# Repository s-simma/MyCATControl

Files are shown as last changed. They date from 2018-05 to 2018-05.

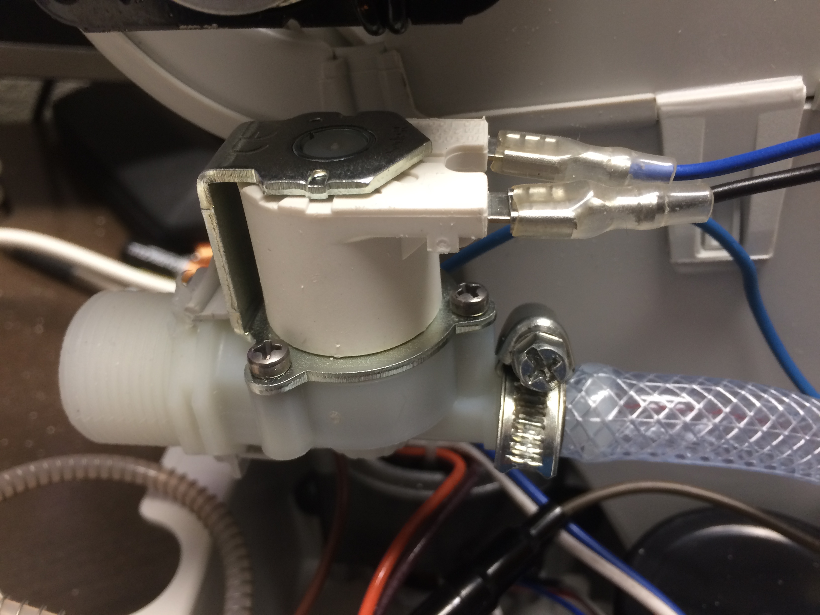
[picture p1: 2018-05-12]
images/IMG_0972.JPG

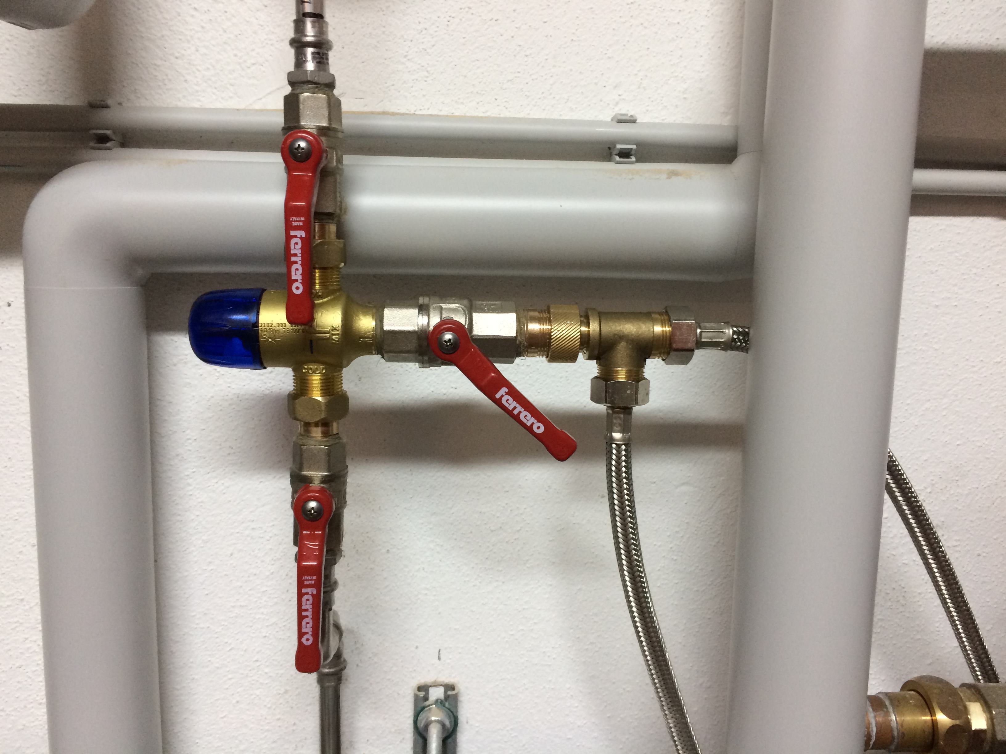
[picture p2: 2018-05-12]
images/IMG_1017.JPG

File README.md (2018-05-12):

## General ##
The reason for this project was to integrate the CAT-toilet "CATGenie120" into my smarthome and to make it possible to lock a toilet while an other one is cleaning.

**The most important for me was:**

- new board replaces the original one

- synchronice 2 or more CATGenies

- integration into my openhab2 smarthome control

- hot water for cleaning

- Using my own admixture to reduce smell

**Design of the controll board:**

- Arduino with WIFI (Genuino MKR1000)

- EEPROM for WEB-Page and cleaning programs (both can be uploaded)

- Real time clock (without power running for at least 1 day)

- Hardware watchdog

- RS485 Interface for syncronisation

##  ##

THE HARWARE DESIGN AND THE SOFTWARE IS PROVIDED "AS IS", WITHOUT WARRANTY OF ANY KIND EXPRESSED OR IMPLIED. IN NO EVENT SHALL THE AUTHOR BE LIABLE FOR ANY CLAIM, DAMAGES OR OTHER LIABILITY.

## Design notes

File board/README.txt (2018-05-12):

I ordered the board:
https://www.eurocircuits.com/

You can directly upload the Eagle .brd file (no gerber files necessary)

Advices for soldering board
---------------------------
You need 3 soldering tips
0,8mm (for IC's)
1,6mm (for resistors, small capacitors)
3,2mm (for relais, power supply, big capacitors)

solder wire 0,5mm and 1mm

a good fix mounted magnifying glass with light

1. Soilder the SMD IC's, transistors (0,8mm)
2. Soilder the SMD resistors + capacitors (1,6mm)
3. Big Components (3,2mm)

As there is nearly no space between the power supply block and the MKR1000
both shoud be soldered together. Otherwise putting the MKR1000 into the sockets could be a problem.

Important !!!!!
Some board connectors seem to be different depending where you bought the CATGenie. (Check it first)

Important !!!!!!
for 110V Version
----------------
F1, R1, R60, R61, C101, C102, C103, R100

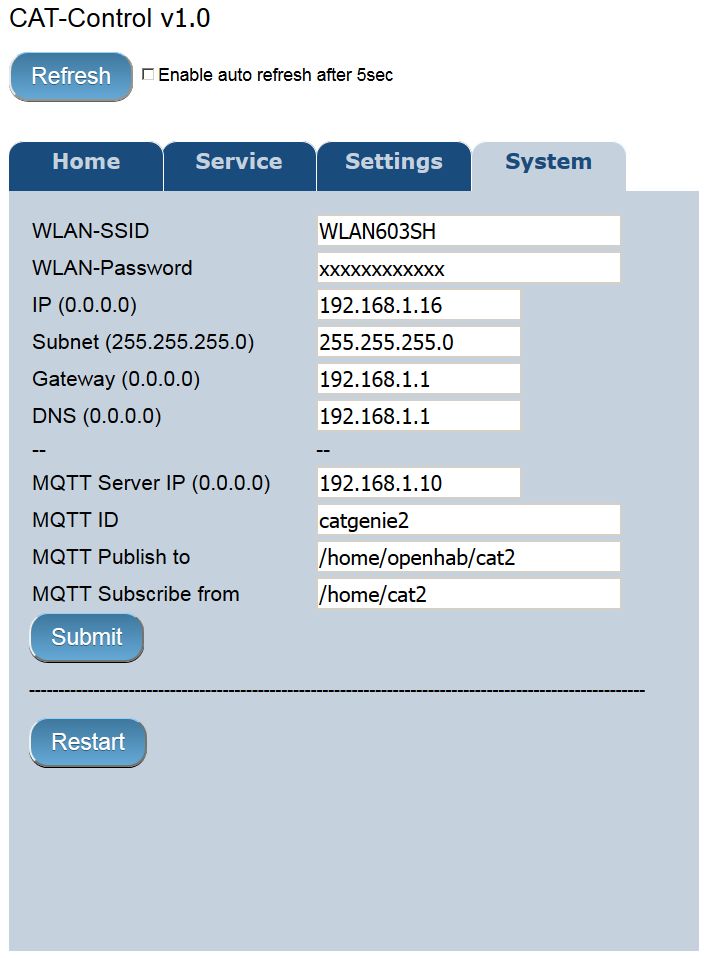
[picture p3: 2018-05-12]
images/WEB_4.jpg

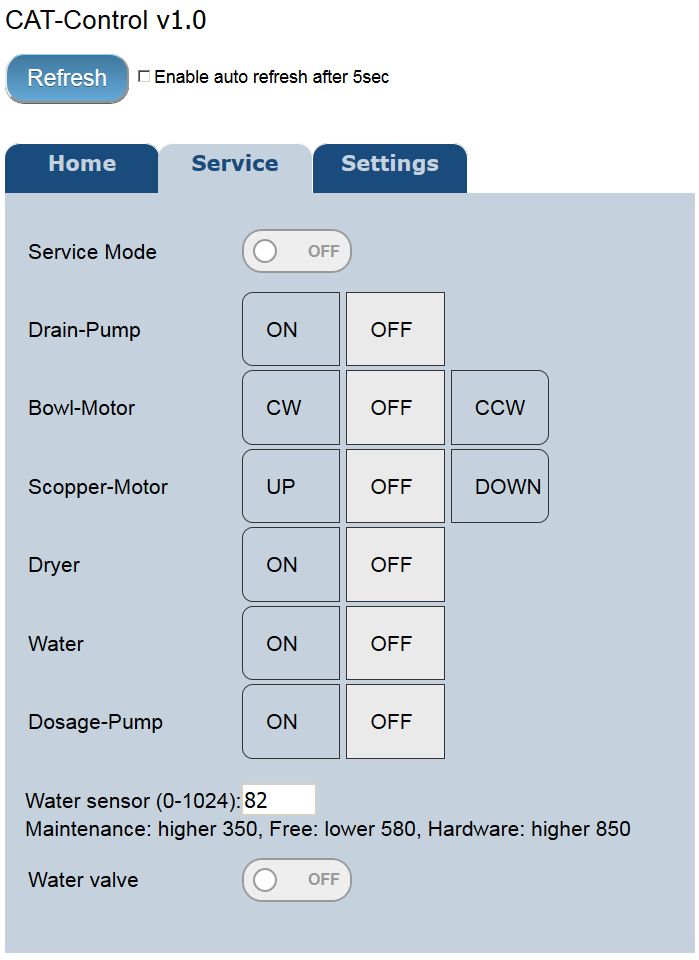
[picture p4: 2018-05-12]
images/WEB_2.jpg

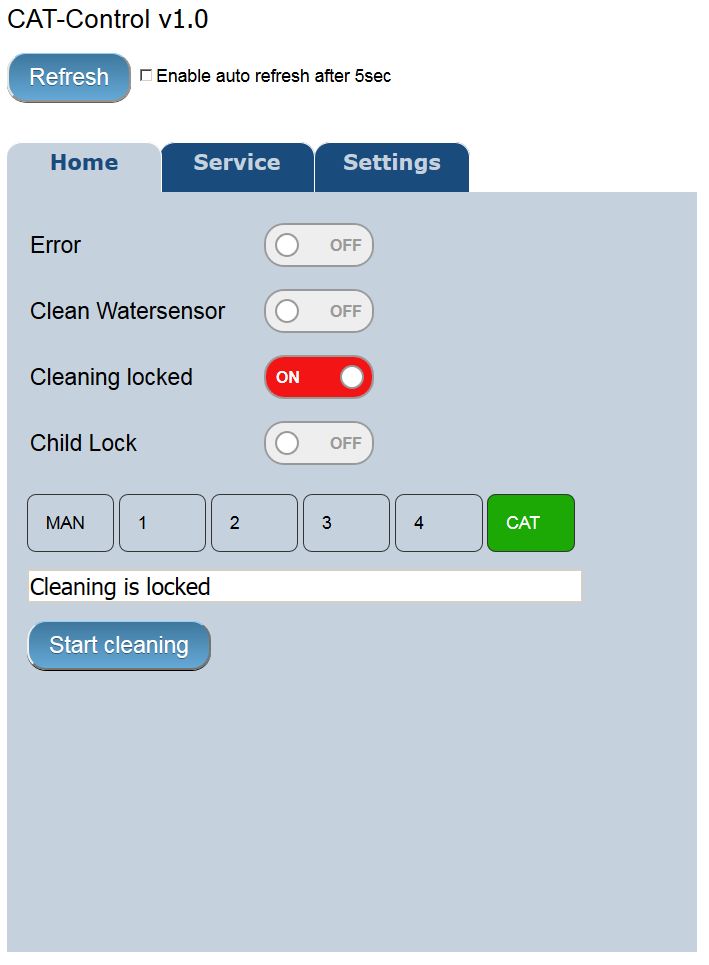
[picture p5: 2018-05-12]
images/WEB_1.jpg

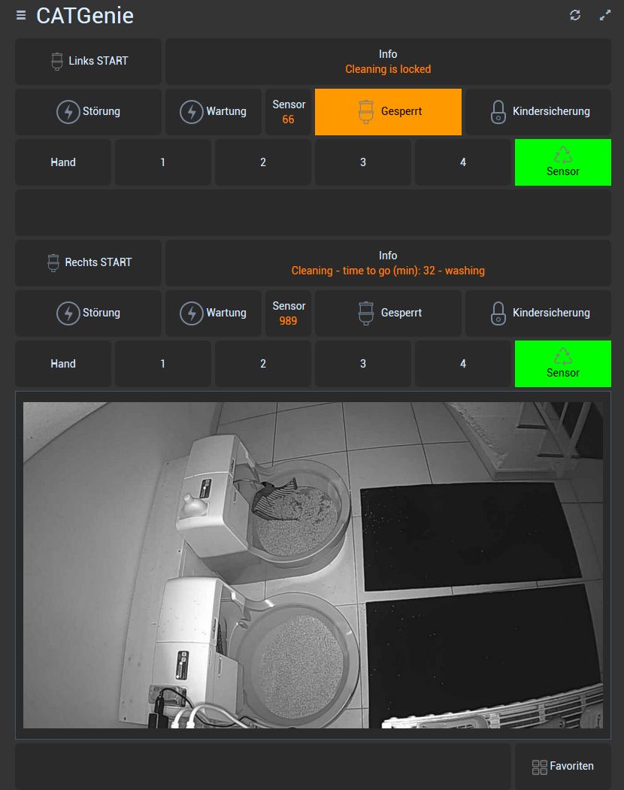
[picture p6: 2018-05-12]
images/SmartHome_4.jpg

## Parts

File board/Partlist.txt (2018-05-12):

Partlist

Exported from CatGenie120.sch at 30.04.2018 11:56

EAGLE Version 7.6.0 Copyright (c) 1988-2016 CadSoft

Assembly variant: 

Part     Value                   Device                  Package                     Library                        Sheet

+3V3                             1,6/0,8                 1,6/0,8                     wirepad                        1
+5V                              1,6/0,8                 1,6/0,8                     wirepad                        1
C1       1000UF                  EEE-FC1C221AP-CASE-G    CAPAE1030X1050N             Panasonic-EEE0_EEE1_EEE2_EEEFC 1
C2       100nF                   C1206C104K5RACTU        CAPC3216X88N                my_library1                    1
C3       47UF                    EEE-0JA470SR-CASE-C     CAPAE530X610N               Panasonic-EEE0_EEE1_EEE2_EEEFC 1
C4       100nF                   C1206C104K5RACTU        CAPC3216X88N                my_library1                    1
C5       100nF                   C1206C104K5RACTU        CAPC3216X88N                my_library1                    1
C6       100nF                   C1206C104K5RACTU        CAPC3216X88N                my_library1                    1
C7       100nF                   C1206C104K5RACTU        CAPC3216X88N                my_library1                    1
C8       100nF                   C1206C104K5RACTU        CAPC3216X88N                my_library1                    1
C9       100nF                   C1206C104K5RACTU        CAPC3216X88N                my_library1                    1
C10      10nF                    C1206C104K5RACTU        CAPC3216X88N                my_library1                    1
C11      1,5F/3,6V               SUPERCAP-RM5            SUPERCAP-RM5                my_library1                    1
C12      100nF                   C1206C104K5RACTU        CAPC3216X88N                my_library1                    1
C13      100nF                   C1206C104K5RACTU        CAPC3216X88N                my_library1                    2
C14      10nF                    C1206C104K5RACTU        CAPC3216X88N                my_library1                    1
C15      100nF                   C1206C104K5RACTU        CAPC3216X88N                my_library1                    1
C16      100nF                   C1206C104K5RACTU        CAPC3216X88N                my_library1                    1
C17      10nF                    C1206C104K5RACTU        CAPC3216X88N                my_library1                    1
C40      47UF                    EEE-0JA470SR-CASE-C     CAPAE530X610N               Panasonic-EEE0_EEE1_EEE2_EEEFC 2
C60      100nF                   C1206C104K5RACTU        CAPC3216X88N                my_library1                    2
C70      100nF                   C1206C104K5RACTU        CAPC3216X88N                my_library1                    2
C71      100nF                   C1206C104K5RACTU        CAPC3216X88N                my_library1                    2
C101     100nF/440V              ANLAUF-KONDENSATOR-RM22 ANLAUF-KONDENSATOR-RM22     my_library1                    2
C102     100nF                   ANLAUF-KONDENSATOR-RM22 ANLAUF-KONDENSATOR-RM22     my_library1                    2
C103     330nF                   ANLAUF-KONDENSATOR-RM37 ANLAUF-KONDENSATOR-RM37     my_library1                    2
D1       1N4148                  DIODE-D-5               D-5                         diode                          1
D51      1N4148                  DIODE-D-5               D-5                         diode                          2
D52      1N4148                  DIODE-D-5               D-5                         diode                          2
D53      1N4148                  DIODE-D-5               D-5                         diode                          2
D54      1N4148                  DIODE-D-5               D-5                         diode                          2
D55      1N4148                  DIODE-D-5               D-5                         diode                          2
D56      1N4148                  DIODE-D-5               D-5                         diode                          2
D57      1N4148                  DIODE-D-5               D-5                         diode                          2
D58      1N4148                  DIODE-D-5               D-5                         diode                          2
D60      1N4004                  1N4004                  DO41-10                     adafruit                       2
F1       10A                     SICHERUNGSHALTER        SICHERUNGSHALTER            my_library1                    1
GND                              1,6/0,8                 1,6/0,8                     wirepad                        1
IC1      LM393D                  LM393D                  SO08                        linear                         2
J1                               JST-EH-03-PIN           JST-EH-03-PIN               JST XH Connectors v1-0         2
J2       5267-6                  5267-6                  5267-6                      con-molex-spox                 2
J3       5267-6                  5267-6                  5267-6                      con-molex-spox                 2
J4                               KK-156-3                KK-156-3                    con-molex                      2
J5                               KK-156-2                KK-156-2                    con-molex                      2
J6       SUPU-SERIE_B_1X3        SUPU-SERIE_B_1X3        SUPU-SERIE_B_1X3            my_library1                    2
J7       JST-XH-02-PIN-ROUND-PAD JST-XH-02-PIN-ROUND-PAD JST-XH-02-PACKAGE-ROUND-PAD JST XH Connectors v1-0         2
J8       JST-XH-05-PIN-ROUND-PAD JST-XH-05-PIN-ROUND-PAD JST-XH-05-PACKAGE-ROUND-PAD JST XH Connectors v1-0         2
J9                               MOLEX-1X3               MOLEX-1X3                   my_library1                    2
J10      MOLEX-1X2               MOLEX-1X2               MOLEX-1X2                   my_library1                    1
J11                              MOLEX-1X3               MOLEX-1X3                   my_library1                    1
JP1                              JP1Q                    JP1                         jumper                         1
MKR1000                          GENUINOMKR1000          GENUINOMKR1000              my_library1                    1
MP       FLACHSTECKER-1POLIG     FLACHSTECKER-1POLIG     FLACHSTECKER-1POLIG         my_library1                    1
O1       G3VM-61G1               MOSFET_RELAIS           MOSFET-RELAIS               my_library1                    2
O2                               MOSFET_RELAIS           MOSFET-RELAIS               my_library1                    2
O3                               MOSFET_RELAIS           MOSFET-RELAIS               my_library1                    2
O4                               MOSFET_RELAIS           MOSFET-RELAIS               my_library1                    2
O5       G3VM-61G1               MOSFET_RELAIS           MOSFET-RELAIS               my_library1                    2
O6                               MOSFET_RELAIS           MOSFET-RELAIS               my_library1                    2
O7                               MOSFET_RELAIS           MOSFET-RELAIS               my_library1                    2
O8                               MOSFET_RELAIS           MOSFET-RELAIS               my_library1                    2
O60      SFH6106-3               SFH6106-3               SFH6106-3                   my_library1                    2
PH       FLACHSTECKER-1POLIG     FLACHSTECKER-1POLIG     FLACHSTECKER-1POLIG         my_library1                    1
Q1       32,768kHz               CRYSTALTC26V            TC26V                       adafruit                       1
R1       VARISTOR-7,5            VARISTOR-7,5            R-7,5                       varistor                       1
R2       10k                     WIEDERSTAND_802         WIEDERSTAND_802             my_library1                    1
R3       3.3k                    WIEDERSTAND_802         WIEDERSTAND_802             my_library1                    1
R4       3.3k                    WIEDERSTAND_802         WIEDERSTAND_802             my_library1                    1
R5       4k7                     WIEDERSTAND_802         WIEDERSTAND_802             my_library1                    1
R6       18k                     WIEDERSTAND_802         WIEDERSTAND_802             my_library1                    1
R7       18k                     WIEDERSTAND_802         WIEDERSTAND_802             my_library1                    1
R8       180R                    R-EU_M1206              M1206                       resistor                       1
R9       150R                    2NBS16-8E               SO16                        resistor-bourns                1
R10      4k7                     WIEDERSTAND_802         WIEDERSTAND_802             my_library1                    1
R11      47k                     WIEDERSTAND_802         WIEDERSTAND_802             my_library1                    1
R40      220R                    WIEDERSTAND_802         WIEDERSTAND_802             my_library1                    2
R41      560R                    WIEDERSTAND_802         WIEDERSTAND_802             my_library1                    2
R42      1k                      WIEDERSTAND_802         WIEDERSTAND_802             my_library1                    2
R43      180R                    R-EU_R1206              R1206                       rcl                            2
R44      4k7                     WIEDERSTAND_802         WIEDERSTAND_802             my_library1                    2
R45      100R                    R-EU_R1206              R1206                       rcl                            2
R46      220R                    WIEDERSTAND_802         WIEDERSTAND_802             my_library1                    2
R47      10k                     WIEDERSTAND_802         WIEDERSTAND_802             my_library1                    2
R51      270R                    R-EU_R1206              R1206                       rcl                            2
R52      270R                    R-EU_R1206              R1206                       rcl                            2
R53      270R                    R-EU_R1206              R1206                       rcl                            2
R54      270R                    R-EU_R1206              R1206                       rcl                            2
R55      270R                    R-EU_R1206              R1206                       rcl                            2
R56      270R                    R-EU_R1206              R1206                       rcl                            2
R57      270R                    R-EU_R1206              R1206                       rcl                            2
R58      270R                    R-EU_R1206              R1206                       rcl                            2
R60      13k/250V/3W             R-EU_R2512              R2512                       rcl                            2
R61      13k/250V/3W             R-EU_R2512              R2512                       rcl                            2
R62      4k7                     WIEDERSTAND_802         WIEDERSTAND_802             my_library1                    2
R63      1M                      WIEDERSTAND_802         WIEDERSTAND_802             my_library1                    2
R70      220R                    WIEDERSTAND_802         WIEDERSTAND_802             my_library1                    2
R71      560R                    WIEDERSTAND_802         WIEDERSTAND_802             my_library1                    2
R72      1k                      WIEDERSTAND_802         WIEDERSTAND_802             my_library1                    2
R73      1k                      WIEDERSTAND_802         WIEDERSTAND_802             my_library1                    2
R74      100k                    WIEDERSTAND_802         WIEDERSTAND_802             my_library1                    2
R75      47k                     WIEDERSTAND_802         WIEDERSTAND_802             my_library1                    2
R76      47k                     WIEDERSTAND_802         WIEDERSTAND_802             my_library1                    2
R77      4k7                     WIEDERSTAND_802         WIEDERSTAND_802             my_library1                    2
R78      220R                    WIEDERSTAND_802         WIEDERSTAND_802             my_library1                    2
R79      220R                    WIEDERSTAND_802         WIEDERSTAND_802             my_library1                    2
R80      560R                    WIEDERSTAND_802         WIEDERSTAND_802             my_library1                    2
R81      1k                      WIEDERSTAND_802         WIEDERSTAND_802             my_library1                    2
R82      200R                    R-EU_R1206              R1206                       rcl                            2
R83      220R                    WIEDERSTAND_802         WIEDERSTAND_802             my_library1                    2
R84      10k                     WIEDERSTAND_802         WIEDERSTAND_802             my_library1                    2
R85      4k7                     WIEDERSTAND_802         WIEDERSTAND_802             my_library1                    2
R86      4k7                     WIEDERSTAND_802         WIEDERSTAND_802             my_library1                    2
R87      47k                     WIEDERSTAND_802         WIEDERSTAND_802             my_library1                    2
R100     2,4k/3W/600V            R-STEHEND               R-STEHEND                   my_library1                    2
RL1                              G6RN-1-5VDC             G6RN-1-5VDC                 my_library1                    2
RL2                              G6RN-1-5VDC             G6RN-1-5VDC                 my_library1                    2
RL3                              G6RN-1-5VDC             G6RN-1-5VDC                 my_library1                    2
RL4                              G6RN-1-5VDC             G6RN-1-5VDC                 my_library1                    2
RL5                              G6RN-1-5VDC             G6RN-1-5VDC                 my_library1                    2
RL6                              G6RN-1-5VDC             G6RN-1-5VDC                 my_library1                    2
RL7                              G6RN-1-5VDC             G6RN-1-5VDC                 my_library1                    2
RL8                              G6RN-1-5VDC             G6RN-1-5VDC                 my_library1                    2
SG1                              PIEZZO-BUZZER1          PIEZZO-BUZZER1              my_library1                    1
T1       BSS138P                 BSS138P                 SOT23                       my_library1                    1
T2       BSS138P                 BSS138P                 SOT23                       my_library1                    1
T40      BSS138P                 BSS138P                 SOT23                       my_library1                    2
T41      IRLML2244               IRLML2244               IRLML2240                   my_library1                    2
T42      BSS138P                 BSS138P                 SOT23                       my_library1                    2
T60      BSS138P                 BSS138P                 SOT23                       my_library1                    2
T70      BSS138P                 BSS138P                 SOT23                       my_library1                    2
T71      IRLML2244               IRLML2244               IRLML2240                   my_library1                    2
T72      BSS138P                 BSS138P                 SOT23                       my_library1                    2
T73      IRLML2244               IRLML2244               IRLML2240                   my_library1                    2
T74      BSS138P                 BSS138P                 SOT23                       my_library1                    2
U$1      PMAS5 S05-L             PMAS5-S05-L             PMAS5-S05L                  my_library1                    1
U1       MCP1825S-3302E/DB       MCP1825S-3302E/DB       MCP1825S-3302E-SOT-223-3    my_library1                    1
U2       24LC512-E/SN            24LC512-E/SN            24LC512-SOIC-8              my_library1                    1
U3       DSS1388                 DSS1388                 DS1388                      my_library1                    1
U4       TLC555CDR               TLC555CDR               TLC555-SOIC-8               my_library1                    1
U5       MCP23S08SO              MCP23S08SO              SO-18W                      microchip-dspic                1
U6       MCP23008SO              MCP23008SO              SO-18W                      microchip-dspic                2
U7       MAX3483ECSA+T           MAX3483                 MAX3483                     my_library1                    1
X1                               PINHD-1X11              1X11                        pinhead                        1

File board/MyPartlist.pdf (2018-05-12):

Tabelle1

Seite 1

Part | Typ | Data | Manufact | Supplier | Order no | Qty | Price
CATControl board | V2.1 | | Eurocircuit | Eurocircuit | | 1 | € 45,00
Genuino MKR1000 | Arduino board with WIFI | | Genuino | http://www.exp-tech.de | EXP-R55-004 | 1 | € 36,88
Board-to-Board Connector | Connector 14 pins, 1 Row | SSQ-114-01-G-S | Samtec | http://at.farnell.com | 1668311 | 2 | € 3,00
Power supply | IN:100-230V, OUT:5V/1A | https://www.mtm-power.com Machatka | PMAS5 S05-L | 1 | € 45,00
X1 (Pin strip for Display) | 1 Row x 36, RM2,54 | 11 pin used | | https://www.reichelt.at | SL 1X36W 2,54 | 0,3 | € 0,21
F1 (Fuse holder) | 25mm x 11mm | RM 22,5, Use fuse: 5x20/max 10A | Schurter, 0031.8201 http://at.farnell.com | 1162740 | 1 | € 0,43
F1 Fuse | 8A middle | 5x20mm | ESKA | https://www.reichelt.at | MTR. 8,0A | 1 | € 0,33
R1 (Varistor) | 250VAC, RM7,5 | B72210S0251K101 | EPCOS | http://at.farnell.com | 1004355 | 1 | € 0,51
RL1 – RL8 (Power Relais) | G6RN-1 5VDC | Print Powerrelais 5V / 114R, 230V/8A | Omron | https://www.distrelec.at | 137-95-010 | 8 | € 4,27
O1 – O8 (MOSFET-Relais) | Mosfet Relais, G3VM-61G1 | 60VAC / 400mA | Omron | https://www.distrelec.at | 171-40-049 | 8 | € 2,34
C103 330nF / 650V MKP, RM27,5 (32x18mm) Kemet https://www.distrelec.at 300-33-188 1 € 3,62 C101, 102 100nF / 650V MKP, RM22,5 (26,5x11mm) Kemet https://www.distrelec.at 300-33-185 2 € 1,28
R100 (Power resistor) | 2.2k, 5Watt, 750V | | | Conrad | 402176-62 | 1 | € 0,96
D60 (Diode high voltage) | 1N4007, DO-41 | Reverse Voltage 1000V, 1A | | http://at.farnell.com | 1843698 | 1 | € 0,19
R60, R61 | 13K | 3W, 250V, 2512, 352213KFT | TE Connectivity | http://at.farnell.com | 2476515 | 2 | € 0,72
O60 (Optocoupler) | SFH6106-3, SO-4 | Optocoupler 5,3kV, 60mA, 70V | Vishay | http://at.farnell.com | 1469572 | 1 | € 0,70
SG1 (Piezzo Buzzer) | | 3V-30V/ Imax=4mA | Multicomp | http://at.farnell.com | 1756516 | 1 | € 0,89
T41, 71, 73 | IRLML2244 | P-Channel MOSFET,-20V/-3,4A | Infinion | http://at.farnell.com | 2468051 | 3 | € 0,30
T1, 2, 40, 42, 60, 70, 72, 74 | BSS138P | N-Channel MOSFET, 60V, 360mA | NXP | http://at.farnell.com | 1859849 | 8 | € 0,29
Q1 (Crystal for U3) | Cylinder 6 x 1,9mm | 32.768kHz, 6pF | CITIZEN | http://at.farnell.com | 1652560 | 1 | € 0,59
U1 (Voltage regulator) | MCP1825S-3302E/DB | In: 2.1-6V, Out: 3,3V/500mA, SOT-223-3 Microchip | http://at.farnell.com | 1578404 | 1 | € 0,49
U2 (EEPROM) | 24LC512-I/SM | I2C, 512Kbit, 64Kx8bit, SOIC-8 | Microchip | http://at.farnell.com | 9758038 | 1 | € 1,50
U3 (Clock&Watchsdog) | DS1388Z-33+T&R | I2C, Realtime clock, Watchdog | Maxim | http://at.farnell.com | 2515475 | 1 | € 4,11
U4 (Oscillator for Buzzer) | TLC555CDR | 2V-15V, SOIC-8 | Texas Instruments | http://at.farnell.com | 8454426 | 1 | € 0,56
U5, U6 (I/O Expander) | MCP23008-E/SO | I2C, VCC 1,8-5,5V, SOIC-18 | Microchip | http://at.farnell.com | 1332086 | 2 | € 0,93
U7 (RS232 – RS422/485) | MAX3483ECSA+T | 3,3V-3,6V, NSOIC-8 | Maxim | http://at.farnell.com | 2512096 | 1 | € 4,43
IC1 (Comperator) | LM393D | 2V-36V, SOIC8 | Texas | http://at.farnell.com | 2294229 | 1 | € 0,39
D1, D51 – D58 (Diode) | 1N4148TR | 100V, 150mA, 4ns | Vishay | http://at.farnell.com | 1469384 | 9 | € 0,09
C1 | EEEFT1C102AP | 1000uF, 16V, 10mm x 10,2mm | Panasonic | http://at.farnell.com | 2065974 | 1 | € 1,27
C3, C40 | EEEFK1C470UR | 47uF, 16V, 5mm x 5,8mm | Panasonic | http://at.farnell.com | 9695664 | 2 | € 0,20
C2,4,5,6,7,8,9,12,13,15,16,60,70,71 C1206C104K5RACTU | 100nF, 50V, +-10%, X7R, SMD 1206 | Kemet | http://at.farnell.com | 1414715 | 12 | € 0,05
C10, 14 | C1206C103K5RACTU | 10nF, 50V, +-10%, X7R, SMD 1206 | Kemet | http://at.farnell.com | 1414713 | 1 | € 0,09
C11 (Goldcap) | EEC-RG0V155VN | 1,5F / 3,6V | Panasonic | Conrad | 1482651-62 | 1 | € 7,59
R40, 46, 70, 78, 79, 83 | 220R | 0,125W, 1%, 150V, 0805 | MULTICOMP | http://at.farnell.com | 2074404 | 6 | € 0,02
R41, 71, 80, | 560R | 0,125W, 1%, 150V, 0805 | MULTICOMP | http://at.farnell.com | 2074483 | 3 | € 0,02
R42, 72, 73, 81 | 1k | 0,125W, 1%, 150V, 0805 | MULTICOMP | http://at.farnell.com | 2073606 | 4 | € 0,02
R3, R4 | 3k3 | 0,125W, 1%, 150V, 0805 | MULTICOMP | http://at.farnell.com | 2074438 | 2 | € 0,02
R5, 10, 44, 62, 77, 85, 86 | 4k7 | 0,125W, 1%, 150V, 0805 | MULTICOMP | http://at.farnell.com | 2073779 | 7 | € 0,02
R2, 47, 84 | 10k | 0,125W, 1%, 150V, 0805 | MULTICOMP | http://at.farnell.com | 2074334 | 3 | € 0,02
R6, R7 | 18k | 0,125W, 1%, 150V, 0805 | MULTICOMP | http://at.farnell.com | 2074387 | 2 | € 0,02

Tabelle1

Seite 2

R11, 75, 76 ,87 | 47k | 0,125W, 1%, 150V, 0805 | MULTICOMP | http://at.farnell.com | 2074470 | 4 | € 0,03
R74 | 100k | 0,125W, 1%, 150V, 0805 | MULTICOMP | http://at.farnell.com | 2073608 | 1 | € 0,02
R63 | 1M | 0,125W, 1%, 150V, 0805 | MULTICOMP | http://at.farnell.com | 2073609 | 1 | € 0,02
R51 – R58 | 270R | 0,25W, 1%, 200V, 1206 | MULTICOMP | http://at.farnell.com | 2074612 | 8 | € 0,02
R8, 43 | 180R | 0,25W, 1%, 200V, 1206 | MULTICOMP | http://at.farnell.com | 2074583 | 1 | € 0,02
R45 | 100R | 0,25W, 1%, 200V, 1206 | MULTICOMP | http://at.farnell.com | 2074536 | 1 | € 0,02
R82 | 200R | 0,25W, 0,1%, 25ppm, 200V, 1206 | Panasonic | Conrad | 1467903-62 | 1 | € 1,19
R9 (Resistor array) | 4816P-T01-151LF | 8 x 150R, Total 1,28W | Bourns | https://www.distrelec.at | 160-32-543 | 1 | € 1,02
USB Connector | USB 2.0 A-Buchse-A-Buchse | Einbau | | https://www.reichelt.at | DELOCK 86317 | 1 | € 6,00
USB Microlink C - A | Von MKR1000 auf Gehäuse | 0,5m weiss | | https://www.reichelt.at | SHVP 77180-W | 1 | € 1,60
RS485 Connector

Connectors for 230V Version
Plug Power supply | PCB 6,3x0,8mm | https://www.distrelec.at | 300-66-559 | 2 | € 0,20
J1 (Dosage) JST EH 1x3, RM 2,5, 250V/3A JST RS-Component 515-1399 1 € 0,18 J2,J3 (Bowl/Scopper) MOLEX SPOX 1x6, RM 2,54, 250V/3A Molex RS-Component 687-8054 2 € 0,08 J4 (Discharge Pump) MOLEX KK 396 1x3, RM 3,96, 250V/7A Molex RS-Component 670-5231 1 € 0,38 J5 (Fan) MOLEX KK 396 1x2, RM 3,96, 250V/7A Molex RS-Component 670-5237 1 € 0,07
J6 (Heater) | SUPU Serie B, 1x3 | 19A/600V | https://www.pollin.at | 451873 | 1 | € 0,75
| J7 (Water valve) JST XH 1x2, RM 2,5, 250V/3A JST RS-Component 820-1554 1 € 0,12
| J8 (CAT-Sensor) JST XH 1x5, RM 2,5, 250V/3A JST RS-Component 820-1560 1 € 0,16
J9 (Water sensor) | MOLEX KK 254 1x3, RM 2,54, 250V/4A Molex RS-Component | 483-8477 1 € 0,19
J10 (RS485) | MOLEX KK 254 1x2, RM 2,54, 250V/4A Molex RS-Component | 483-8461 1 € 0,19
J11 (Option) | MOLEX KK 254 1x3, RM 2,54, 250V/4A Molex RS-Component | 483-8477 1 € 0,19

Connectors for 110V Version
Plug J2 (Scopper) | JST XH6P ST | 1x6, RM 2,5, 250V/3A | JST | https://www.reichelt.at | JST XH6P ST | 1 | € 0,26
Plug J1 (Dosage pump) | JST XH3P ST | 1x3, RM 2,5, 250V/3A | JST | https://www.reichelt.at | JST XH3P ST | 1 | € 0,16
Plug J7 (Water valve) | JST XH2P ST | 1x2, RM 2,5, 250V/3A | JST | https://www.reichelt.at | JST XH2P ST | 1 | € 1,10
Plug J3 (Bowl) | JST EH6P ST | 1x6, RM 2,5, 250V/3A | JST | https://www.reichelt.at | JST EH6P ST | 1 | € 0,22
Plug J5 (Heater van) | JST VH2P ST | 1x2, RM 3,96, 250V/10A | JST | https://www.reichelt.at | JST VH2P ST | 1 | € 0,13
Plug J4 Drain pump | JST VH3P ST | 1x3, RM 3,96, 250V/10A | JST | https://www.reichelt.at | JST VH3P ST | 1 | € 0,19

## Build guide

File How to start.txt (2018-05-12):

Install Arduino IDE (i used 1.6.13) on your computer
Select board MKR1000

copy libraries to Arduino LIB Folder
.....\Documents\Arduino\libraries

Update to latest board version (in IDE)

!!!!!Important !!!!!!
---------------------
Update WIFI Firmware to version 19.5.4
do NOT update this LIB-Files !!!!

Adjust Arduino sketch "CATControl.ino"
--------------------------------------
#define WLAN_SSID "My_WLAN_SSID"
#define WLAN_PASSWD "My_WLAN_Password"
#define NET_IP "192.168.1.17"
#define NET_SNM "255.255.255.0"
#define NET_GW "192.168.1.1"
#define NET_DNS "192.168.1.1"

// Date / Time
#define TIMEOFFSET 1               // Time offset (h) +/- for your time-zone
#define USEDST true                // Use sommer/wintertime (adjust time in summer +1h)

-----

Upload Arduino sketch to the board
----------------------------------
After startup there should be a short beep and the Error LED should go on. Quitt the error by pressing the START/AUTO Button.

Upload WEB-Page to the (WIFI)
---------------------------------
Execute "TCPSendFile.jar" (Set Board IP, Select WEB-Page: index1_compressed.html)
Max WEB-Page size: 39kByte -> index.html should be compressed before download
You can use this compressor: https://htmlcompressor.com/compressor/

Upload cleaning programs to arduino (WIFI)
------------------------------------------
Execute "TCPSendFile.jar" (Set Board IP, Select tasklist: e.g. Full_1.txt)
Max 5 tasklists (1-5)
Max. 390 lines / tasklist

During upload, it make sense to enable the monitor in the arduino IDE (at least for the first time)

WEB-Page for configuration
--------------------------
use Firefox: http://192.168.1.17:8080
You should see the WEB-Page now

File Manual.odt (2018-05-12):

Manual CAT-Control

After power-on → LED test

After Startup → Beep → Error LED ON (Error code = 99)

If you don't press the START Button within 3 minutes (confirm the startup), the CATControl switch to CAT-sensor mode and checks if an active cleaning cycle was interrupted by a power-down.

if NO goto :continue

if YES and settings „Tasklist after power-on if water is in the bowl“ is zero, goto :continue

if YES and cleaning cycle was interruped during scooping -> start cycle with tasklist assigend to CAT-sensor mode

if YES and cleaning cycle was interruped during washing or drying -> start cycle with tasklist entered in settings -> „Tasklist after power-on if water is in the bowl“

:continue

I. Modes

Standard Mode (CARTRIGE-LED = off, CHILD-LOCK-LED = off)

AUTO Click → switch to program (1,2,3,4,CAT)

START Click → Start / Stop cleaning precess

Service Mode (CARTRIDGE-LED = BLINKING)

(from standard mode)

AUTO Longpress + START DoubleClick → Enter service mode (stop cleaning program if running)

AUTO Click → Select output

1 = Drain pump

2 = Bowl

3 = Scopper

4 = Dryer

4 + 1 = Water

4 + 2 = Dosage pump

START Click → switch selected output (1, off, 2)

AUTO Longpress → Exit service mode → reset all outputs

START Longpress → Run into watchdog → all LED's ON → restart after 1 minute

Child Lock (CHILD-LOCK LED = ON)

(from standard mode)

AUTO + START Longpress → Childlock on

AUTO + START Longpress → Childlock off

Lock CATGenie (CARTRIGE-LED = on)

(from standard mode)

START Double-Click to enable

START Double-Click to disable

If CATGenie is more than 1 hour locked, it will unlock automtically.

II. Error Display (ERROR LED = ON)

Error codes (1-7) are shown on the panel in binary form (LED1-LED4)

e.g. Error 1 = LED1, Error 7 = LED4+LED3

Error Codes:

1 Water sensor needs cleaning

2 Water in Bowl on start cleaning

3 Water discharge problem

4 Dryerfuse broken

5 Tasklist not 1-3

6 EEProm tasklist error

9 Unknown error „doCATGenie()“

10 Unknown error „myCATGenie.startCleaning(tasklist)“

11 Error manually set by browser

12 Error manually set by MQTT

99 Power up

A clean watersensor should display an analog value between 50 and 100.

III. Erease Configuration parameter, tasklists and WEB-Page

Press AUTO and START button during LED-Test

-> Errror LED goes ON

-> After EEProm ereased (about 10s) Error LED will flush

Power on/off or wait 60s for watchdog to restart the program with its default values.

IV. Tasklist

* Each tasklist must be a plain ASCII text file

* The first two lines must be

<CATGenie>

tasklist start 1

* the last line must be

tasklist end

* Descriptions have to start with „//“ (No discriptions allowed after a command !!!!)

// Comment

Max. 390 command lines are allowed per tasklist

Max. 5 tasklists are allowed

Possible commands

wait 0.6 (seconds)

bowl ccw

bowl cw

bowl stop

scopper up

scopper stop

scopper down

drainpump on

drainpump stop

dospump on

dospump stop

water on

water is on

water waitin 70 (seconds)

water stop

water waitout 1 (seconds)

dryer on

dryer stop

V. What should be improved

- validate tasklist file before download (java downloader)
- check max. web-page size before download (java downloader)

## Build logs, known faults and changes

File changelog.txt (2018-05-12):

10.5.2018 v1.1
CAT-In detection handled now with "OneButton" in loop
(easier to detect false positive)

21.12.2017
v1.0 Initial version

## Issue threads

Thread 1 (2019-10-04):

confused about input voltage

vileer, 2019-10-04:
hi simma, just a little confused about the working voltage. In the schematic pdf file the input voltage is 230V, but you mentioned it is designed for 110V in the readme.txt. So is it working under 230V or 110V?

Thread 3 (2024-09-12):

USA BOM

HipMusicman, 2024-09-12:
This might not be the right place for this but I really wanted to post an updated BOM for this project.
All of the parts should be direct replacements.
This BOM excludes some of the things like cables and the 230V Version items so make sure you don't miss those.

Here is also a link to the DigiKey cart with updated qtys for some added scrap and cost savings:
https://www.digikey.com/short/b2n8z0pq

Please note, the Arduino will need to be purchased elsewhere as DigiKey does not have stock of them.

myList:
[MyPartlist_USA.xlsx](https://github.com/user-attachments/files/16979970/MyPartlist_USA.xlsx)
BOM:
[MyPartlist.xlsx](https://github.com/user-attachments/files/16979971/MyPartlist.xlsx)

Duron27, 2024-09-12:
I ended up using an 8 relay board and have everything setup in homeassistant. only issue is I have to manually do everything since I couldn't get the code to port to an esp32

Duron27, 2024-09-12:
no I didn't even try it, I just didnt want to order a custom board and wanted to try a simple 8 relay board. I have a water sensor and the auto button at the top connected, thats it. but again it can't run a cycle or anything, I need to manually open and close the relays

PhilGillam, 2024-09-12:
That would make sense as one board is an arduino and the other is an esp32, they have different outputs and inputs as well as different access to memory and the RTC.
However you can take the Arduino code and use it as a template to write code for the esp32

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

PhilGillam, 2024-09-12:
Im not sure why you would try a relay board, its like putting switches on all the outputs and sitting there toggling switches while watching the cat t*rd floating round and round.

You need a controller, this can be a Arduino, esp32 or a raspberry pi – then code running for the automation

So simma has done this for you, get the board, load the Arduino code and it runs, failing this go and get melkors project which was designed for an esp32, however there is no code, so you will need to code from scratch
CatGenie - OSHWLab<https://oshwlab.com/melkor/catgenie>

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

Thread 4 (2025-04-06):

Webpage causing crash and restart

HipMusicman, 2025-04-06:
Any interaction with the webpage causes a crash and device restart.

After struggling trying to get the Arduino to even connect to wifi, I'm finally now to the point were the compressed html and the Full_1 tasklist are uploaded to the EEPROM.

Any interaction with the webpage returns this in the Serial Monitor:
WEB-Server: Received POST request
LEN HTTP-Header: 79
POST /outputChange HTTP/1.1
Host: 192.168.0.17:8080
Connection: keep-alive
C

My intuition is it's crashing, but I'm completely lost as to why.

[sketch_apr6a.zip](https://github.com/user-attachments/files/19622897/sketch_apr6a.zip)

HipMusicman, 2025-04-06:
This seems to be a chrome/brave issue (since they both are Chromium).

Firefox does work when interacting with the catgenie without crashing but does not show the current state. Chrome and Brave will however.
I'm since this was built using an older version of Firefox, it is no longer compatible with the latest version.

HipMusicman, 2025-04-07:
I got it working with the latest version of Firefox.
Filling out all fields in the System tab did the trick.
Basically, Firefox could not determine the values past "pass" and everything below and including "ipadr" could not be understood.

Chrome and Brave do not work because the buffer size is not large enough and crashes. At least that's how I understand it. Increasing the limit from 80 to 256 lets us see more data in the Serial Monitor before it crashes but it's still not enough.

I've reset the EEPROM, removed the following values from the Sketch file:

  // During waiting WIFI101 calls doCATGenie()
  WiFi.setWaitCallback(doCATGenie);
  // During waiting Pubsubclient calls doCATGenie()
  mqttclient.setWaitCallback(doCATGenie);

Then I set the necessary network values, uploaded the compressed html and task files and now it seems to be working.

Next on the list is actually putting everything through it's paces.

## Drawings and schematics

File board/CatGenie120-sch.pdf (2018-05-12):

# CAT_v2.3

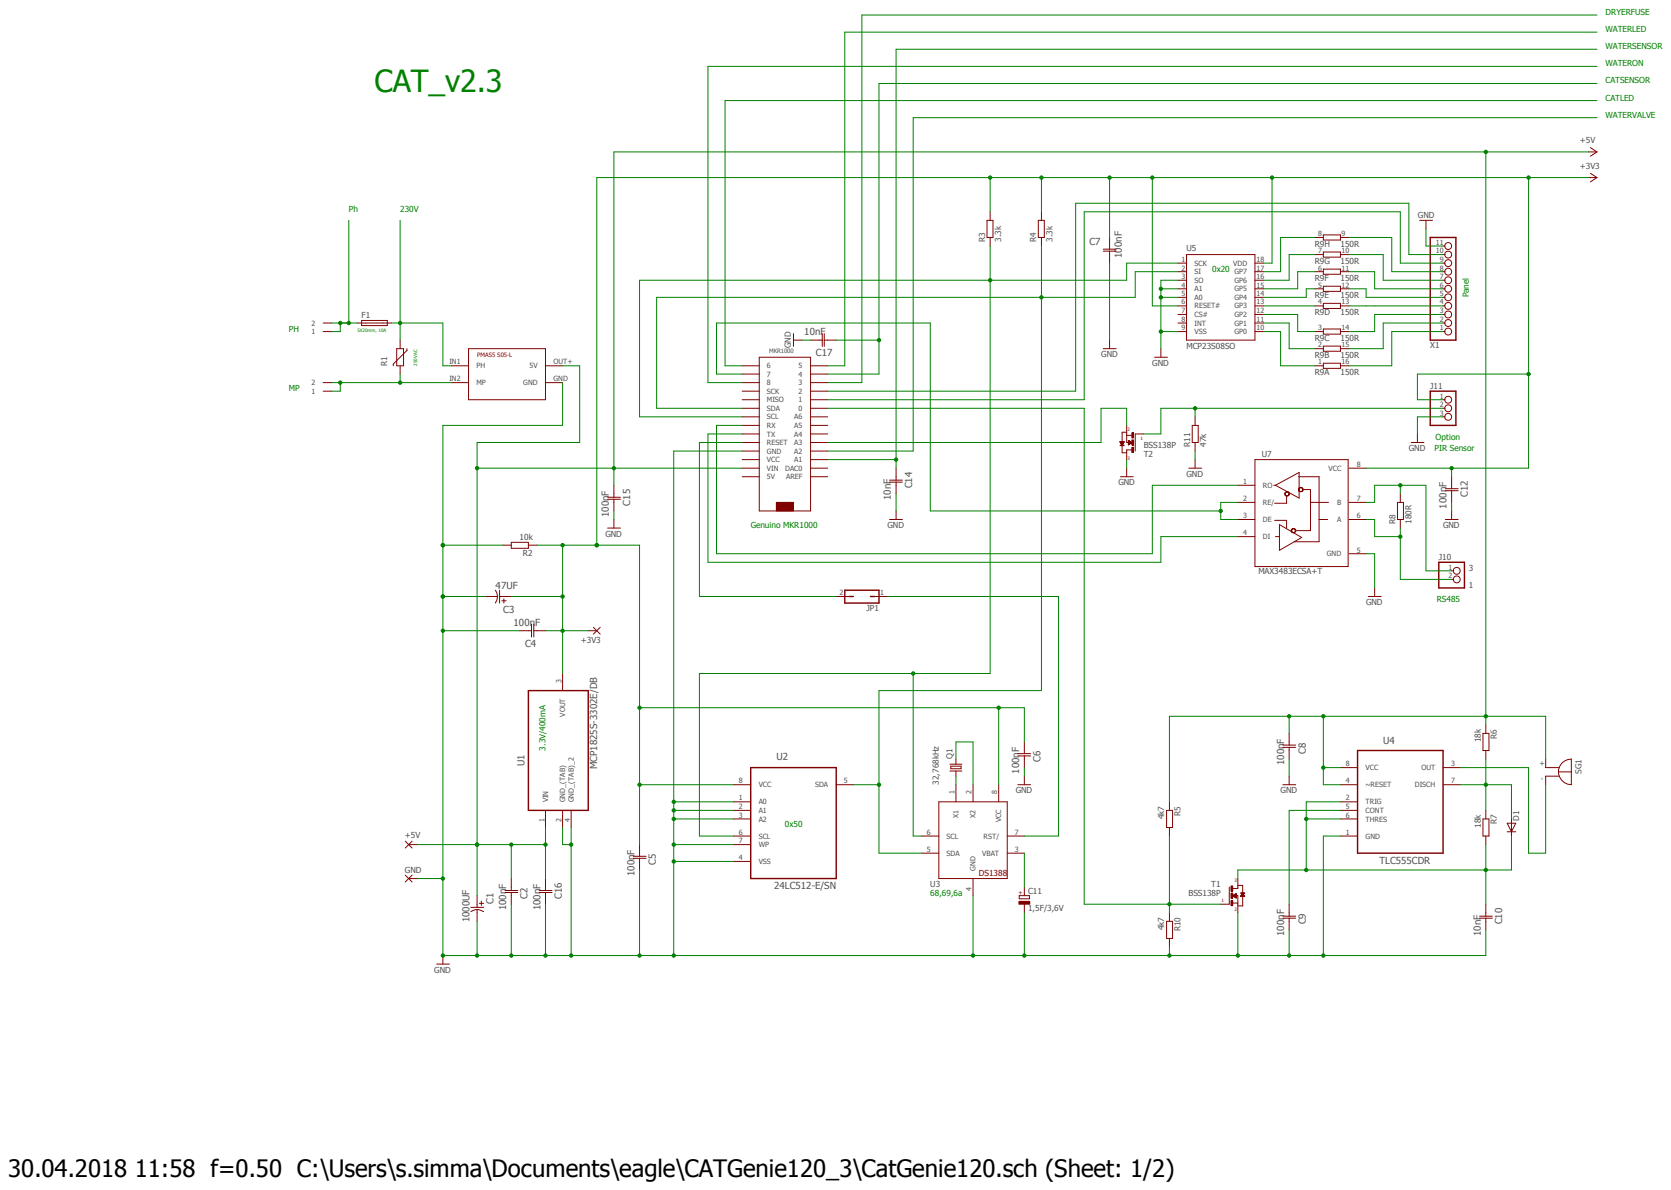
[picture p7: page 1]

30.04.2018 11:58 f=0.50 C:\Users\s.simma\Documents\eagle\CATGenie120_3\CatGenie120.sch (Sheet: 1/2)

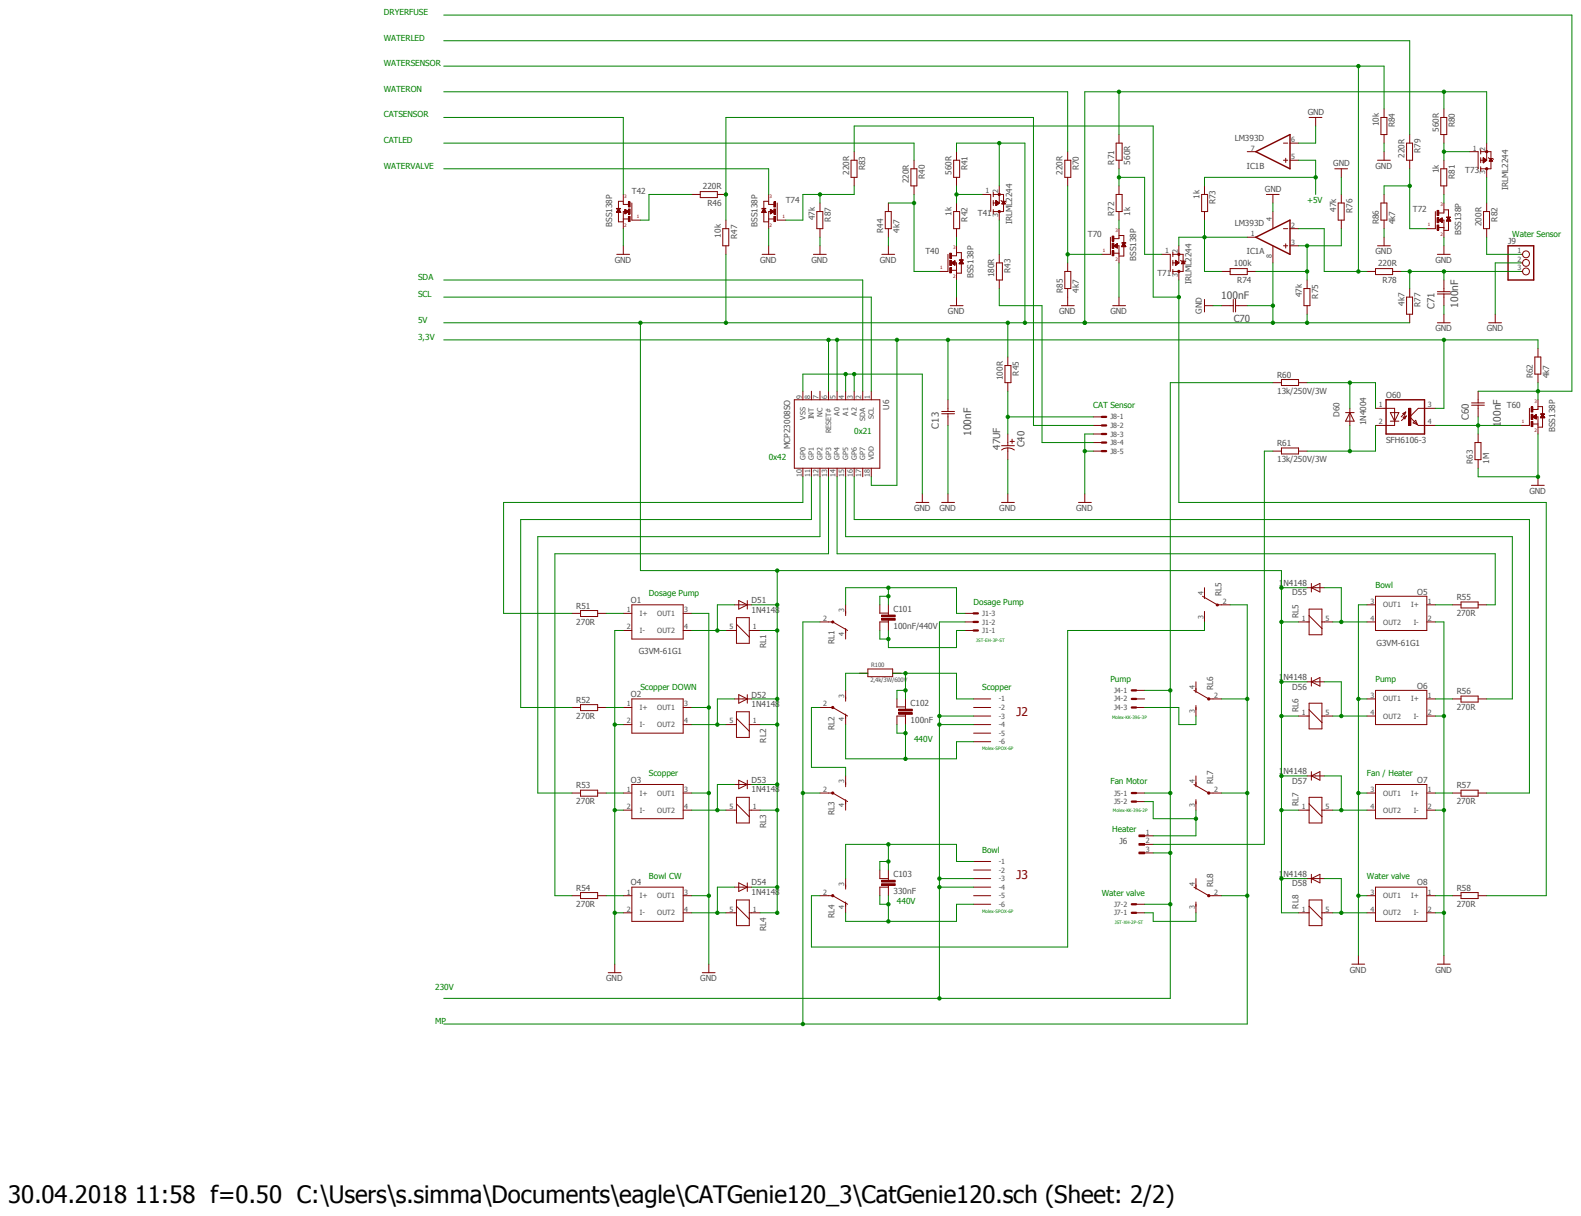
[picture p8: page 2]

30.04.2018 11:58 f=0.50 C:\Users\s.simma\Documents\eagle\CATGenie120_3\CatGenie120.sch (Sheet: 2/2)

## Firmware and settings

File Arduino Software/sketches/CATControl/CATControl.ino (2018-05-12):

#define PRGVERSION "v1.0"

/////////////////////////////////////////////////////////////////////////////////////////////////////////////////////
// Use Arduino IDE: 1.6.13
// copy lib-folder into documents\arduino folder (do not update lib's)
//
// Download WEB-page to MKR1000 (use my TCPSendFile.jar -> enter ip of the MKR1000 -> select html File)
// Download Cleaning Program.txt file to MKR1000 (use my TCPSendFile.jar -> enter ip of the MKR1000 -> select txt File)
// Use Firefox as Browser http://<ip of the MKR1000>:8080
// 
// -------- You have to adjust these values and download sketch afterwards -----------------------
// Date / Time
#define TIMEOFFSET 1                    // Time offset (h) +/- for your time-zone
#define USEDST true                     // Use sommer/wintertime (adjust time in summer +1h)

// WIFI
#define WLAN_SSID "WLANSSID"	        // WLAN SSID
#define WLAN_PASSWD "123456"	        // WLAN Password
#define NET_IP "192.168.1.17"           // 0.0.0.0 for DHCP (can be changed with Browser)
#define NET_SNM "255.255.255.0"
#define NET_GW "192.168.1.1"
#define NET_DNS "0.0.0.0"               // Not used

// MQTT
#define MQTT_SERVER_IP "0.0.0.0"              // MQTT Server IP Adresse
#define MQTT_ID "catgenie"                    // MQTT ID
#define MQTT_PUBLISH "/home/openhab/cat"      // Publish to
#define MQTT_SUBSCRIBE "/home/cat"            // Subscribe from


// ===============================================================================================
// ===============================================================================================
// I2C
#include <Wire.h> 

// Realtime clock / watchdog
#include <DS1388.h>

// WIFI
#include <WiFi101.h>

// MQTT
#include <PubSubClient.h>

// Threads
#include <Thread.h>
#include <ThreadController.h>

// Bounce inputs
#include <Bounce2.h>

//Handle buttons AUTO/START
#include <OneButton.h>   

// CATGenie
#include <CATGenie.h>

// DS1388 object
rtcDS1388 rtc1388;

// EEPROM
extEEPROM eep(kbits_512,1,64,EEP_ADDR);  // device size, number of devices, page size

// Threads
ThreadController threadController = ThreadController();
Thread thread1 = Thread();
Thread thread2 = Thread();

//Handle Long/Short press AUTO/START buttons
OneButton btnAuto(BUTTON_AUTO, true); 
OneButton btnStart(BUTTON_START, true);

//Input CATSensor activated 
OneButton inpCATSensor(CATSENSOR, false);


#define WEBSERVER_PORT 8080               // Port to listen for show WEB Page
#define SAVEWEB_PORT 7002                 // Port to listen (for save WEB Page to EEProm)

// WEB Server
WiFiServer WEBserver(WEBSERVER_PORT);

// WEB Page
WiFiServer EEPServer(SAVEWEB_PORT);      // receive WEB-page over tcp -> EEProm

// MQTT Client
WiFiClient mqttnet;                      // For send data to server
PubSubClient mqttclient(mqttnet);        // MQTT client

// RS485 receive command buffer
int rs485Pointer = 0;
char rs485Buffer[80];

// General variables
boolean doRestart = false;              // Restart MKR1000 (command from WEB-Browser)
uint16_t wbTypeId = 0;                  // command from the WEB-Browser
boolean wbAutoRefresh = false;          // autorefresh from the WEB-Browser
uint8_t restartCounter = 0;             // second Counter for autostart cleaning after power up or restart
volatile boolean runCatGenie = false;   // Run CATGenie Object in Loop (Set in Timer4 Interrupt) 

boolean catSensInp = false;             // CAT sensor input (OneButton) 
boolean catIn = false;                  // CAT is in
unsigned long catInTime = 0;            // CAT In Timer
unsigned long catOutTime = 0;           // CAT Out Timer

unsigned long lastCleaningTime = 0;     // Last cleaning time
boolean cleanLocked = false;            // Start cleaning locked by other CAT Genie
uint8_t cleanLockedTime = 0;            // For reset Clean-Lock after MAXCLEANLOCK
boolean childLock = false;              // Lock panel
uint8_t cleanProgram = 0;               // Actual cleaning program
uint16_t cleanDelay = 0;                // After delay expired start clean (triggered by CATSENSOR)
boolean cleanPending = false;           // Clean Pending
uint8_t inService = 0;                  // 0=Not in service mode, 1=scopper, 2=BOWL....
uint8_t inServiceState = 0;             // last actor state when in service (0,1,2)
uint8_t catError = 0;                   // Error status 1=Maintenence, 2=Water fill problem, 3=Drain problem, 4=Dryer Fuse, 98=unknown error
int progId;
boolean sendMQTTServer = false;
boolean checkDryerFuse = false;
uint8_t lastCleaningState = 0;          // last cleaning state 0=not clening, 1=scooping, 2=washing, 3=drying (for handle power restart)
uint8_t servWatSens = 0;                // Minute counter for service water sensor

// System Configuration stored in EEProm
// If this structure is changed -> delete config area in EEProm (0-1023)
// Use Browser to enter settings again
typedef struct {
  uint16_t lenstruct;                     // !!!! must be the first

  char ssid[32] = WLAN_SSID;              // your network SSID (name)
  char pass[16] = WLAN_PASSWD;            // your network password
  char ip_adr[16] = NET_IP;               // IP
  char subnet[16] = NET_SNM;              // Subnet
  char gateway_ip[16] = NET_GW;           // Gateway
  char dnsserver_ip[16] = NET_DNS;        // DNS Server

  char mqttid[32] = MQTT_ID;                         // ID
  char topic_Publish[32] = MQTT_PUBLISH;             // Publish to
  char topic_Subscribe[32] = MQTT_SUBSCRIBE;         // Subscribe to

  int utcTimeoffs = TIMEOFFSET;
  boolean useDST = USEDST;

  uint16_t catTimeIn = CATINTIME;
  uint16_t cleanDelay = CLEANDELAY;
  uint16_t forceCleaning = FORCECLEAN;

  char mqttserver[16] = MQTT_SERVER_IP;
  uint8_t lockHHfrom = 0;
  uint8_t lockMMfrom = 0;
  uint8_t lockHHto = 0;
  uint8_t lockMMto = 0;

  uint8_t lock2HHfrom = 0;
  uint8_t lock2MMfrom = 0;
  uint8_t lock2HHto = 0;
  uint8_t lock2MMto = 0;

  uint8_t taskl_pow = 0;

  uint8_t prog_man = PROGM;
  uint8_t prog_1 = PROG1;
  uint8_t prog_2 = PROG2;
  uint8_t prog_3 = PROG3;
  uint8_t prog_4 = PROG4;
  uint8_t prog_cat = PROGC;
} confStruct;
confStruct confData[1];


// ----------------------------------------------- SETUP BEGIN ----------------------------------------------------------------
void setup() {

  int i;
  byte ipadr[4];
  
  //Init BUZZER
  pinMode(BUZZER,OUTPUT);
  digitalWrite(BUZZER,HIGH);

  //Initialize serial and wait for port to open
  Serial.begin(9600);
  delay(2000);

  // Init Interface between multiple CATGenie's (RS485)
  // Switch RS485 to read data
  pinMode(RS485RW,OUTPUT);
  digitalWrite(RS485RW,LOW);
  Serial1.begin(9600);
  delay(2000);  

  // Set I2C as a Bus-Master
  Wire.begin();

  // Configure Threads
  thread1.onRun(Monitor_1);
  thread1.setInterval(1000);          // 1 Sekunde
  threadController.add(&thread1);
  thread2.onRun(Monitor_60);
  thread2.setInterval(1*60*1000);     // 1 Minute
  threadController.add(&thread2);

  // Test Time is valid (if not -> set default time)
  if (!rtc1388.isrunning()) {
    Serial.println(F("Realtime is not valid -> set default time to compile time"));  
    rtc1388.adjust(DateTime(__DATE__, __TIME__));
    digitalWrite(BUZZER,LOW);
    delay(2000);  
    digitalWrite(BUZZER,HIGH);
  }

  Serial.println(F("Actual date/time: "));    
  DateTime actDate = rtc1388.now(confData[0].utcTimeoffs, confData[0].useDST);      
  Serial.print(actDate.day(), DEC);
  Serial.print('.');
  Serial.print(actDate.month(), DEC);
  Serial.print('.');
  Serial.print(actDate.year(), DEC);
  Serial.print(' ');
  Serial.print(actDate.hour(), DEC);
  Serial.print(':');
  Serial.print(actDate.minute(), DEC);
  Serial.print(':');
  Serial.print(actDate.second(), DEC);
  Serial.println();  
 
  // Enable watchdog
  Serial.println(F("Enable Watchdog: 30s"));
  rtc1388.startWatchdogTimer(30,0);  
 
  // Enable Trickle charger
  Serial.println(F("Enable Trickle Charger 250R / no Diode"));
  rtc1388.setTrickleCharger(1);  
    
  // Get CATGenie Configuration from EEProm
  i = eep.read(0, (byte*)confData, 2);
  // Do we have a valid configuration
  if ((i == 0) && (confData[0].lenstruct == sizeof(confData))) {
    i = eep.read(0, (byte*)confData, sizeof(confData));
    if (i != 0) {
      Serial.println(F("Error: Could not read configuration from EEProm -> use default ........"));    
    }
  } else {
    Serial.println(F("Error: No valid configuration in EEProm -> use default ........"));        
    confData[0].lenstruct = sizeof(confData);    
    i = eep.write(0, (byte*)confData, sizeof(confData));
    Serial.print(F("Configuration file written size: "));
    Serial.println(sizeof(confData));
  }

  // Initialize CATGenie object (must be done before using CATGenie object)
  myCATGenie.begin();
            

  // Wait 3 seconds for Auto/Start buttons together -> Set default IP and disable server
  unsigned long startWait = millis();
  while (getDiffTime(startWait, millis()) < 3000) {
    if ((digitalRead(BUTTON_AUTO) == LOW) && (digitalRead(BUTTON_START) == LOW)) {
      Serial.println(F("......Erease EEProm............"));  
      myCATGenie.setOutput(LED_ERROR);
      eeErase(64, 0, 64 * 1024 - 1);
      boolean isOn = false;
      while (true) {
        if (isOn) {
          myCATGenie.resetOutput(LED_ERROR);
          isOn = false;                    
        } else {
          myCATGenie.setOutput(LED_ERROR);
          isOn = true;          
        }
        delay(500);
      }      
    }
  }
 
  // link the AUTO-button to the Handler
  btnAuto.setDebounceTicks(50);
  btnAuto.setClickTicks(400);
  btnAuto.attachClick(AutoClick);
  btnAuto.attachDoubleClick(AutoDoubleClick);
  btnAuto.attachLongPressStart(AutoLongPress);

  // link the START-button to the Handler
  btnStart.setDebounceTicks(50);
  btnStart.setClickTicks(400);
  btnStart.attachClick(StartClick);
  btnStart.attachDoubleClick(StartDoubleClick);
  btnStart.attachLongPressStart(StartLongPress);

  // link the START-button to the Handler
  inpCATSensor.setDebounceTicks(20);
  inpCATSensor.attachClick(CatSensorActiv);

  //Control CATLED output for CATSENSOR input
  tc5Configure(69000); //configure the timer to run at <34500*2>Hertz
  tc5StartCounter(); //starts the timer
  
  // Initilize CAT-Sensor input
  pinMode(CATSENSOR, INPUT_PULLUP);

  // Timer4 to handle CATGenie object timers
  tc4Configure(10); //configure the timer to run at 0,1s = 10
  tc4StartCounter(); //starts the timer

  updatePanel(0);

  // Initilize WIFI + MQTT
  myCATGenie.setOutput(LED_ERROR);
  // Give Alarm if WIFI not available
  if (WiFi.status() == WL_NO_SHIELD) {
    Serial.println(F("!!!!!!!!!!WiFi module not present"));
    digitalWrite(BUZZER,LOW);
    delay(4000);  
    digitalWrite(BUZZER,HIGH);
  }

  // Connect to WIFI
  if (strlen(confData[0].ssid) > 0) {          
    ConnectToWIFI();
  }

  // Keine Übertragung zu MQTT Server
  parseBytes(confData[0].mqttserver, '.', ipadr, 4, 10);
  if (((ipadr[0] > 0) && (ipadr[0] < 255))) {
    mqttclient.setCallback(mqtt_callback);
    mqttclient.setServer(confData[0].mqttserver, 1883);
    ConnectToMQTT();  
  }
  lastCleaningTime = millis();
  
  catError = 99;    // Restart
  myCATGenie.setOutput(LED_ERROR);

  // Get the state where the last cleaning was interrupted by power down (Byte 0 from Timer-EEProm)
  lastCleaningState = rtc1388.EEPROMRead(0);
  
  sendToMQTTServer();

  // Setup complete set BUZZER 0,5s
  digitalWrite(BUZZER,LOW);
  delay(500);  
  digitalWrite(BUZZER,HIGH);

  // During waiting WIFI101 calls doCATGenie()
  WiFi.setWaitCallback(doCATGenie);
  // During waiting Pubsubclient calls doCATGenie()
  mqttclient.setWaitCallback(doCATGenie);
}

// ----------------------------------------------- SETUP END ----------------------------------------------------------------


// ----------------------------------------------- LOOP BEGINN ----------------------------------------------------------------
void loop() {
  
  // Restart requested from WEB-Browser
  if (doRestart == true) {
    doRestart = false;
    Serial.println(F("......Wait for watchdog to restart MKR1000............"));  
    myCATGenie.resetOutputAll();    
    myCATGenie.setOutput(LED_ERROR);
    while (true) {}      
  }
  
  // Trigger Watchdog
  rtc1388.resetWatchdogTimer();  
  
  // Handle commands from RS485
  rs485Handler();
  
  // Handle buttons AUTO and START
  btnAuto.tick();
  btnStart.tick();

  // Save the actual cleaning state for power restart (Byte 0 in Timer-EEProm)
  // 0=not cleaning, 1=scooping, 2=washing, 3=drying
  if (catError != 99) {
    uint8_t isState = myCATGenie.isCleaning();
    if (isState != lastCleaningState) {
      lastCleaningState = isState;
      // write new state to EEProm
      rtc1388.EEPROMWrite(0,lastCleaningState);                  
    }
  }
  
  // Handle CATSensor
  inpCATSensor.tick();  
  if (catSensInp == true) {
    // Restart clean delay if already running
    if (cleanDelay != 0) {
      cleanDelay = confData[0].cleanDelay;
    } else {
      // The first time sets CAT is in
      if (catIn == false) {
        catIn = true;
        catInTime = millis();
        catOutTime = catInTime;
        updatePanel(0);
        if (confData[0].catTimeIn == 0) {
          cleanDelay = confData[0].cleanDelay;      
          sendMQTTServer = true;                          
        }
      } else {
        catOutTime = millis();
        if (getDiffTime(catInTime,catOutTime) >= (confData[0].catTimeIn * 1000)) {
          cleanDelay = confData[0].cleanDelay;      
          updatePanel(0);
          sendMQTTServer = true;                
        }
      }
    }
    catSensInp = false;
  } else if ((catIn == true) && (getDiffTime(catOutTime, millis()) > (CATMONTIME*1000))) {      
    clearCatIn();
    updatePanel(0);
  }

  // Call CatGenie Object as often as possible
  doCATGenie();
  
  // Handle tasks
  threadController.run();

  // Handle WEB Server
  handleWEBServer();

  // Handle receive WEB-page
  receiveEEPData();

  // Update MQTT server
  mqttclient.loop();
  if (sendMQTTServer == true) {
    sendMQTTServer = false;
    sendToMQTTServer();    
  }
}
// ----------------------------------------------- LOOP END ----------------------------------------------------------------



//////////////////////////////////////////////////////////////////////////
//
// Task Monitor (every second)
//
//////////////////////////////////////////////////////////////////////////
void Monitor_1() {
  uint16_t output;
  
  // Monitor DRYERFUSE if Dryer is ON (after 1 second)
  if (myCATGenie.getOutput(DRYER) == HIGH) {
    if ((checkDryerFuse == true) && (digitalRead(DRYERFUSE) != LOW)) {
      setError(4);    
    }
    checkDryerFuse = true;
  } else {
    checkDryerFuse = false;    
  }
    
  // Update actual state of output in service mode
  if (inService > 0) {
    switch (inService) {
      case 1:
        output = DRAIN_PUMP;
        break;
      case 2:
        output = BOWL;
        break;
      case 3:
        output = SCOPPER;
        break;
      case 4:
        output = DRYER;
        break;
      case 5:
        output = WATERON;
        break;
      case 6:
        output = DOSAGE_PUMP;
        break;
      default:
        return;
    }
    updatePanel(output);    
  }
}

//////////////////////////////////////////////////////////////////////////
//
// Task Monitor (every minute)
//
//////////////////////////////////////////////////////////////////////////
void Monitor_60(){

  char charBuf[64];
  byte ipadr[4];
  boolean reconnect = false;
  IPAddress ip;
  
  // Autostart cleaning after power up or restart
  if (catError == 99) {
    if ((lastCleaningState != 0) && (confData[0].taskl_pow != 0)) {
      restartCounter = restartCounter + 1;
      if (restartCounter >= 3) {
        setCleanProg(5);
        cleanDelay = 1;     // Start power on cleaning process
      }
    } else {
      setCleanProg(5);
      resetError();
      Serial.println(F("Cleaning was not interrupted or no tasklist spezified for power up"));      
    }
  }
  
  // Force clean after n hours not started
  if ((cleanProgram == 5) && (confData[0].forceCleaning != 0)) {
    if (getDiffTime(lastCleaningTime, millis()) >= (confData[0].forceCleaning * 3600 * 1000)) {
        if (cleanDelay == 0) {
          cleanDelay = 1;     // Start cleaning process
        }
    }
  }
  
  // Start Clean process after delay (triggered by CATSENSOR)
  if (cleanDelay > 0) {
    cleanDelay = cleanDelay - 1;
    if (cleanDelay == 0) {
      if ((timeLocked() == false) && (cleanLocked == false)) {
        startCleaning();
      } else {
        cleanPending = true;
        updatePanel(0);        
      }
    }    
  } else {
    if ((cleanPending == true) && (cleanLocked == false) && (timeLocked() == false)) {
      startCleaning();
    }
  }
  
  // Reset Clean locked after Max Time
  if (cleanLocked == true) {
    cleanLockedTime = cleanLockedTime + 1;
    if (cleanLockedTime > MAXCLEANLOCK) {
      resetCleanLock();  
    }
  }

  // Monitor Watersensor -> Check if it needs cleaning
  if ((catError != 99) && (myCATGenie.isCleaning() == 0) && (inService == 0)) {        
    if (myCATGenie.getWaterSensor() > SENSSERVICE) {
      if (servWatSens < SENSSERVTIME) {
        servWatSens = servWatSens + 1;
        if (servWatSens == SENSSERVTIME) {
          setError(1);
        }        
      }
    } else {
      servWatSens = 0;
      if (catError == 1) {
        resetError();                      
      }
    }
  }

  // Test WIFI available
  if (strlen(confData[0].ssid) > 0) {          
    // Only if cleaning process not running
    if (myCATGenie.isCleaning() == 0) {      
      if (WiFi.status() != WL_CONNECTED) {
        Serial.println(F("WIFI is not connected!...try to connect"));
        ConnectToWIFI();
      }       

      // Test ping to gateway
      if (WiFi.status() == WL_CONNECTED) {
        ip = WiFi.gatewayIP();
        if ((ip[0] > 0) && (ip[0] < 255)) {
          if (WiFi.ping(ip) < 0) {
            Serial.println(F("No ping to gateway possible!...try to connect"));
            ConnectToWIFI();
          }
        }
              
        // Test MQTT Connection
        parseBytes(confData[0].mqttserver, '.', ipadr, 4, 10);
        if ((ipadr[0] > 0) && (ipadr[0] < 255)) {      
          if (WiFi.status() == WL_CONNECTED) {
            if (!mqttclient.connected()) {
              Serial.println(F("MQTT is not connected!...try to connect"));
              ConnectToMQTT();
            }
          }
        }
      }
    }  
    // Send actual state to MQTT server
    sendMQTTServer = true;
  }
/*
  byte *ptr = (byte*)malloc(5000);
  if (ptr == NULL) {
    Serial.println("malloc failed..........................");
  } else {
    Serial.println("malloc succeeded.......................");
    free(ptr);
  }
*/  
}


///////////////////////////////////////////////////////
//  Run CatGenie Object every 100ms (Timer4)
///////////////////////////////////////////////////////
void doCATGenie() {
  if (runCatGenie == true) {
    runCatGenie = false;

    // Wait for cleaning process finished
    if (myCATGenie.runL() == true) {
      int i = myCATGenie.getError();
      if (i != 0) {    
        myCATGenie.resetOutputAll();    
        switch (i) {
          case 1:
            setError(2);   // Water fill problem
            break;
          case 2:
            setError(3);   // Water discharge problem
            break;
          default:
            setError(9);   // unknown error
            break;      
        }
      }
      setIdleState();
    }
  }
  return;      
}

///////////////////////////////////////////////////////
//  Set CATGenie is idle
///////////////////////////////////////////////////////
void setIdleState() {

  servWatSens = 0;
  clearCatIn();
  cleanPending = false;
  cleanDelay = 0;
  lastCleaningTime = millis();

  // Send "free" to other CATGenie's
  digitalWrite(RS485RW,HIGH);   // Set RS485 write enable
  Serial1.println("status=free");
  Serial1.flush();
  digitalWrite(RS485RW,LOW);   // Set RS485 read enable
  Serial.println(F("Cleaning FINISHED..............."));
  updatePanel(0);
  sendMQTTServer = true;      
}


//////////////////////////////////////////////////////////////////////////
// Determines if we are inside a global time lock for cleaning 
//////////////////////////////////////////////////////////////////////////
boolean timeLocked() {
  uint16_t fromTime;
  uint16_t toTime;
  uint16_t actTime;
  
  DateTime thisDT = rtc1388.now(confData[0].utcTimeoffs, confData[0].useDST);
  actTime = thisDT.hour()*60 + thisDT.minute();

  // Locktime 1
  fromTime = confData[0].lockHHfrom*60 + confData[0].lockMMfrom;
  toTime = confData[0].lockHHto*60 + confData[0].lockMMto;  
  if (fromTime != toTime) {
    if (toTime > fromTime) {
      if ((actTime >= fromTime) && (actTime < toTime)) {
        return true; 
      }
    } else {
      if ((actTime >= fromTime) || (actTime < toTime)) {
        return true; 
      }    
    }
  }
  
  // Locktime 2
  fromTime = confData[0].lock2HHfrom*60 + confData[0].lock2MMfrom;
  toTime = confData[0].lock2HHto*60 + confData[0].lock2MMto;  
  if (fromTime != toTime) {
    if (toTime > fromTime) {
      if ((actTime >= fromTime) && (actTime < toTime)) {
        return true; 
      }
    } else {
      if ((actTime >= fromTime) || (actTime < toTime)) {
        return true; 
      }    
    }
  }
  return false;
}


//////////////////////////////////////////////////////////////////////////
// CAT-Sensor input activated
// (OneButton callback)
//////////////////////////////////////////////////////////////////////////
void CatSensorActiv() {
  // Activate CAT sensor if program 5 and not cleaning
  if ((cleanProgram == 5) && (myCATGenie.isCleaning() == 0)) {
    catSensInp = true;
  }
}
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
